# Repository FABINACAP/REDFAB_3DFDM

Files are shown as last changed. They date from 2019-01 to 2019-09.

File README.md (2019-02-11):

# REDFAB_3DFDM
REDFAB 3D FDM, es la primera impresora de la familia REDFAB. Diseñada y fabricada por el equipo de Fab INACAP. Es una impresora de código abierto, disponible para cualquier persona que quiera aprender e introducirse en el mundo de la fabricación digital.

El corazón de la REDFAB se compone de un Ardunio Mega , Ramps versión 1.4/1.5, 4 driver Pololu A4988 y manejado bajo el excelente Firmware Marlin V2.0.

Su estructura es de MDF3mm y un set de piezas impresas en PLA.
La REDFAB 3d FDM, se encuentra siempre en mejora continua.

impresoras

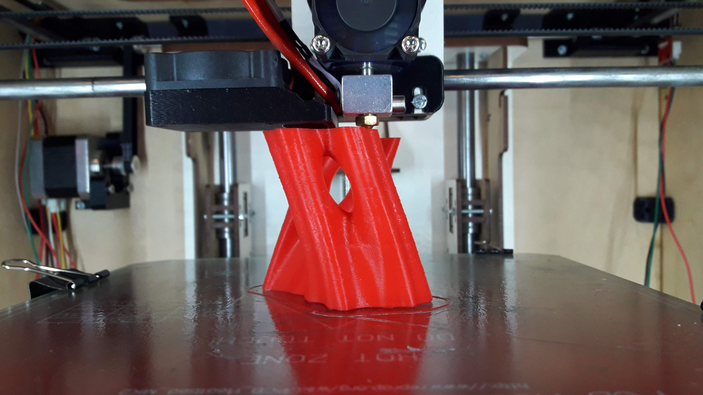
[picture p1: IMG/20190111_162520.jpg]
Test


Una impresora 3D desarrollada por el equipo de Fab INACAP CC-BY-SA-4.0 / An open source 3D printer developed by Fab INACAP team CC-BY-SA-4.0.

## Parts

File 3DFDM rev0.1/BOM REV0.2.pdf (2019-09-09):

# BOM REDFAB 3D FDM

V1.1

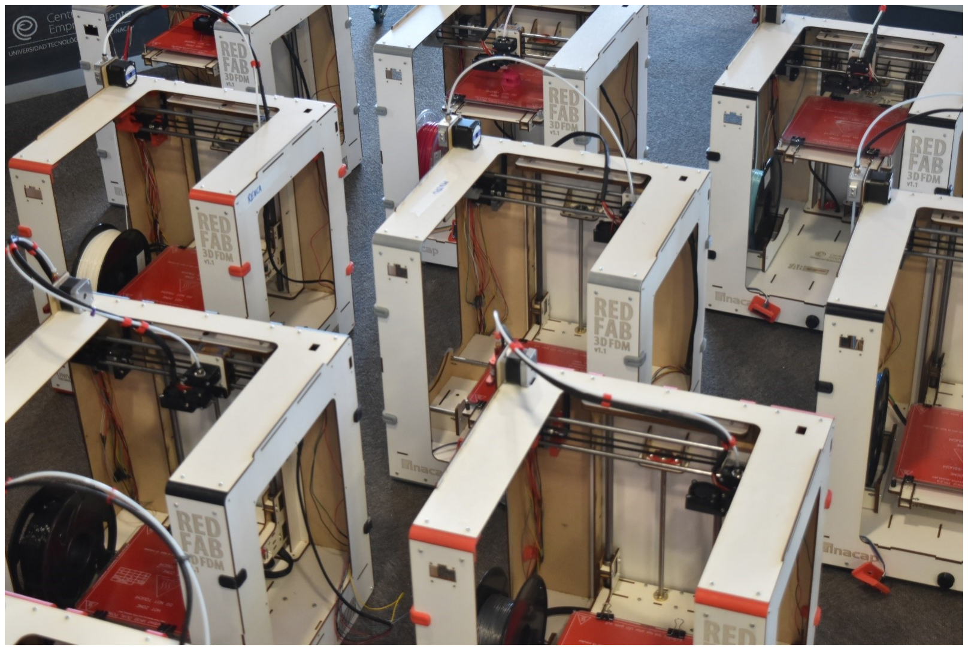
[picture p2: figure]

## Inacap

fabinacap@inacap.cl

### Lista de componentes mecánicos, electrónicos e imprimibles REDFAB 3D FDM v1.1

COMPONENTES MECÁNICOS | CANTIDAD | ITEM
685ZZ, Rodamiento de bolas (5 x 11 x 5mm) | 4
623ZZ, Rodamiento de bolas (3 x 10 x 4mm) | 6
Base Vidrio 21.5 x 21.5cm, e=4mm, chaflan 1cm | 1
LM08UU, Rodamiento lineal de bolas recirculantes (8mm) | 8
LM12UU, Rodamiento lineal de bolas recirculantes (12mm) | 4
Polea dentada GT2-16 (16 dientes) (D.I. 5mm) (B máx: 6mm) | 5
Correa dentada GT2-6 (goma con refuerzo fibra de vidrio) | 3mt
Correa cerrada GT2-6 200mm (goma con refuerzo fibra de vidrio) | 1
Varilla Roscada (husillo) 8mm x 300mm + Tuerca Tr8*4 | 1
Acople rígido de aluminio (5mm a 8mm) | 1
Resorte para cama caliente (ID=5mm, OD=7.5mm, h=20mm) | 4
Conector tubo neumático (para tubo pasante) PC4-01 | 1
Tubo teflón (OD=4mm, ID=2mm), Longitud 1 metro | 1
Tuerca M3 para apretar con la mano | 4
Barra acero trefilado (calidad 1020) 8mm x 385mm (+0.00 -2.00mm) | 2
Barra acero trefilado (calidad 1020) 8mm x 400mm (+0.00 -2.00mm) | 2

## Inacap

fabinacap@inacap.cl

Barra acero trefilado (calidad 1020) 12mm x 400mm (+0.00 -2.00mm) | 2
Barra redonda acero plata 5mm x 390mm (+1.00 -2.00mm) | 1
Durolac Blanco MDF 3mm (cortado en trozos 80x130cm) | 1
Clip doble 15mm, pequeños para fijación de base de vidrio | 4
Amarra Cable 2,5mm largo 140 color negro (Pack 25un) | 1
Pernos y Tuercas | CANTIDAD | ITEM
Tuercas M3 | 150
Pernos Cocina Cabeza Punta cruz M3x10 | 30
Pernos Cocina Cabeza Punta cruz M3x12 | 30
Pernos Cocina Cabeza Punta cruz M3x15 | 30
Pernos Cocina Cabeza Punta cruz M3x20 | 30
Pernos Cocina Cabeza Punta cruz M3x25 | 30
Pernos Cocina Cabeza Punta cruz M3x30 | 30
Pernos Cocina Cabeza Punta cruz M3x35 | 10
Pernos Parker Cabeza Cilíndrica M3x15 | 3
Pernos Cocina Cabeza Punta cruz M4x10 | 4
Golilla Plana Zincada M3 | 10

## Inacap

fabinacap@inacap.cl

COMPONENTES ELECTRÓNICOS | CANTIDAD | ITEM
Arduino Mega 2560 R3 (versión compatible) | 1
Ramps 1.5 o superior | 1
A4988, driver motor paso a paso | 5
Motor PAP bipolar NEMA 17 (3,45V, 1.5A, 45N.cm, 1.8°) Cable 1m removible | 4
Pantalla LCD Oled 1.3" I2C, color blanco | 1
Módulo lector tarjetas SD | 1
Módulo encoder rotatorio | 1
Final de carrera horizontal con PCB + cables | 3
Cama caliente 214 x 214 mm MK2 (Voltaje entrada 12V o 24V) | 1
Termistor NTC 100K 3950 con cable 1 metro | 2
Ventilador 4010 12V (40x40x10mm) | 3
MK8 extrusor remoto de aleación de aluminio para filamento 1.75mm | 1
Fuente Meanwell LRS-350-12 (12V, 29A, 350W) | 1
Conector C14 interruptor con fusible 220V 2A | 1
Cable de poder para PC 1.5m | 1

## Inacap

fabinacap@inacap.cl

COMPONENTES ELECTRÓNICOS | CANTIDAD | ITEM
Cable USB B macho a USB A B hembra para montaje 30cm | 1
Cable USB 2.0 cobre TIPO A-B impresora 1.5m | 1
Diodo 1N4004 o 1N4008 | 2
Extrusor E3D V6 + Ventilador, Boquilla 0,4mm 1,75mm | 1
Memoria SD 8Gb clase 10 | 1
Manga trenzada para cables (8mm expandible) | 3mt
Pack 127 fundas termo retráctiles varios tamaños | 1
Terminal Faston hembra (azul) | 10
Terminal Horquilla 4.4mm (azul) | 10
Pack 40 cables Dupont hembra 30cm | 1
Cordon 3x0.75mm2 | 0.5mt
Cable Evaflex H07Z21-K 2.5mm, (2m color rojo, 2m color verde) | 4mt
Cable AWG 26 colores rojo, negro, gris, amarillo, verde, blanco. (3mt de c/u) | 18mt
Cable AWG 20 (color rojo) | 3mt
Cabezal 2 pines para conector Dupont (paso 2.54mm) | 10
Cabezal 3 pines para conector Dupont (paso 2.54mm) | 10

## Inacap

fabinacap@inacap.cl

Cabezal 4 pines para conector Dupont (paso 2.54mm) | 10
Conectores Dupont hembra (paso 2.54mm) (terminales) | 100
Filamento 1kg PLA 1,75mm (color a elección) | 1

## Inacap

fabinacap@inacap.cl

COMPONENTES IMPRESOS PLA, color a elección | CANTIDAD | ITEM
Eje_X_polea • Imprimir con soporte • Altura de capa 0.2mm • Numero de paredes 3 • Capas Inferior/Superior 4 • Relleno 25%) | 1
Eje_X_Soporte_Motor • Imprimir con soporte • Altura de capa 0.2mm • Numero de paredes 3 • Capas Inferior/Superior 4 • Relleno 25%) | 1

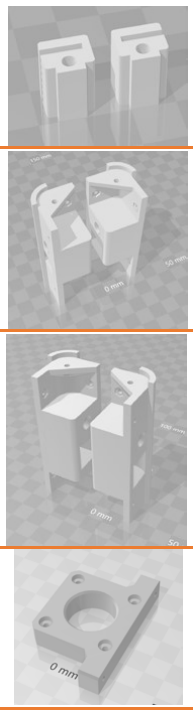
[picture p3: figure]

Tensor Correa un par • Imprimir sin soporte • Altura de capa 0.1mm • Numero de paredes 3 • Capas Inferior/Superior 4 • Relleno 90%) | 1
Eje_Y_Frontal • Imprimir con soporte • Altura de capa 0.2mm • Numero de paredes 3 • Capas Inferior/Superior 4 • Relleno 25%) | 1
Eje_Y_Posterior • Imprimir con soporte • Altura de capa 0.2mm • Numero de paredes 3 • Capas Inferior/Superior 4 • Relleno 25%) | 1
Soporte_Motor_Y • Imprimir sin soporte • Altura de capa 0.2mm • Numero de paredes 3 • Capas Inferior/Superior 4 • Relleno 25%) | 1

## Inacap

fabinacap@inacap.cl

Union_Marcos_Inferior • Imprimir sin soporte • Altura de capa 0.2mm • Numero de paredes 3 • Capas Inferior/Superior 4 • Relleno 25%) | 4
Union_Marcos_posterior • Imprimir sin soporte • Altura de capa 0.2mm • Numero de paredes 3 • Capas Inferior/Superior 4 • Relleno 25%) | 1
Carro_Cabezal • Imprimir sin soporte • Altura de capa 0.2mm • Numero de paredes 3 • Capas Inferior/Superior 4 • Relleno 25%) | 1
Tensor_Correa_Cabezal • Imprimir sin soporte • Altura de capa 0.1mm • Numero de paredes 3 • Capas Inferior/Superior 4 • Relleno 100%) | 1
Soporte_FAN_Layer • Imprimir sin soporte (Recomendación Imprimir en ABS) • Altura de capa 0.2mm • Numero de paredes 3 • Capas Inferior/Superior 4 • Relleno 25%) | 1
Soporte_Hotend • Imprimir sin soporte • Altura de capa 0.2mm • Numero de paredes 3 • Capas Inferior/Superior 4 • Relleno 25%) | 1

## Inacap

fabinacap@inacap.cl

Pantalla_Oled 1.3” • Imprimir sin soporte • Altura de capa 0.2mm • Numero de paredes 2 • Capas Inferior/Superior 3 Relleno 25%) | 1
Clamp • Imprimir sin soporte • Altura de capa 0.2mm • Numero de paredes 3 • Capas Inferior/Superior 4 • Relleno 25%) | 1
Conector_de_Planos • Imprimir sin soporte • Altura de capa 0.2mm • Numero de paredes 3 • Capas Inferior/Superior 4 • Relleno 25%) | 8
Polea_rodamientoB623ZZ_V2 • Imprimir con soporte • Altura de capa 0.1mm • Numero de paredes 3 • Capas Inferior/Superior 2 • Relleno 100%) | 3
Clip cable • Imprimir sin soporte • Altura de capa 0.2mm • Numero de paredes 3 • Capas Inferior/Superior 2 • Relleno 25%) | 1
Rueda_Ajuste_Base (opcional, en remplazo de Tuerca M3 para apretar con la mano) • Imprimir sin soporte • Altura de capa 0.2mm • Numero de paredes 3 • Capas Inferior/Superior 4 • Relleno 25%) | 4
Rueda_Encoder • Imprimir sin soporte • Altura de capa 0.2mm • Numero de paredes 3 • Capas Inferior/Superior 4 • Relleno 25%) | 1

## Inacap

fabinacap@inacap.cl

End_Stop_X_Soporte
- Imprimir sin soporte
- Altura de capa 0.2mm
- Numero de paredes 2
- Capas Inferior/Superior 4 Relleno 25%)

1

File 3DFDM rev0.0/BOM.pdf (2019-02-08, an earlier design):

# BOM REDFAB 3D FDM

V1.1


## Inacap

fabinacap@inacap.cl

### Lista de componentes mecánicos, electrónicos e imprimibles REDFAB 3D FDM v1.1

COMPONENTES MECÁNICOS | CANTIDAD | ITEM
KFL08, Soporte ovalado con rodamiento (8mm) | 2
685ZZ, Rodamiento de bolas (5 x 11 x 5mm) | 2
623ZZ, Rodamiento de bolas (3 x 10 x 4mm) | 6
Base Vidrio 21.5 x 21.5cm, e=4mm, chaflan 1cm | 1
LM08UU, Rodamiento lineal de bolas recirculantes (8mm) | 8
LM12UU, Rodamiento lineal de bolas recirculantes (12mm) | 4
Polea dentada GT2-16 (16 dientes) (D.I. 5mm) (B máx: 6mm) | 5
Correa dentada GT2-6 (goma con refuerzo fibra de vidrio) | 3mt
Correa cerrada GT2-6 200mm (goma con refuerzo fibra de vidrio) | 1
Varilla Roscada (husillo) 8mm x 300mm + Tuerca Tr8*4 | 1
Acople rígido de aluminio (5mm a 8mm) | 1
Resorte para cama caliente (ID=5mm, OD=7.5mm, h=20mm) | 4
Conector tubo neumático (para tubo pasante) PC4-01 | 1
Tubo teflón (OD=4mm, ID=2mm), Longitud 1 metro | 1
Tuerca M3 para apretar con la mano | 4

## Inacap

fabinacap@inacap.cl

Barra acero trefilado (calidad 1020) 8mm x 385mm (+0.00 -2.00mm) | 2
Barra acero trefilado (calidad 1020) 8mm x 400mm (+0.00 -2.00mm) | 2
Barra acero trefilado (calidad 1020) 12mm x 400mm (+0.00 -2.00mm) | 2
Barra redonda acero plata 5mm x 360mm (+1.00 -2.00mm) | 1
Durolac Blanco MDF 3mm (cortado en trozos 80x130cm) | 1
Clip doble 15mm para fijación de base de vidrio | 4
Amarra Cable 2,5mm largo 140 color negro (Pack 25un) | 1

## Inacap

fabinacap@inacap.cl

Pernos y Tuercas | CANTIDAD | ITEM
Tuercas M3 | 150
Tuercas M5 | 4
Pernos Cocina Cabeza Punta cruz M3x10 | 30
Pernos Cocina Cabeza Punta cruz M3x12 | 30
Pernos Cocina Cabeza Punta cruz M3x15 | 30
Pernos Cocina Cabeza Punta cruz M3x20 | 30
Pernos Cocina Cabeza Punta cruz M3x25 | 30
Pernos Cocina Cabeza Punta cruz M3x30 | 30
Pernos Cocina Cabeza Punta cruz M3x35 | 10
Pernos Parker Cabeza Cilíndrica M3x15 | 3
Pernos Cocina Cabeza Punta cruz M4x10 | 4
Pernos Cocina Cabeza Punta cruz M5x12 | 4
Golilla Plana Zincada M3 | 20

## Inacap

fabinacap@inacap.cl

COMPONENTES ELECTRÓNICOS | CANTIDAD | ITEM
Arduino Mega 2560 R3 (versión compatible) | 1
Ramps 1.4 o superior | 1
A4988, driver motor paso a paso | 5
Motor PAP bipolar NEMA 17 (3,45V, 1.5A, 45N.cm, 1.8°) Cable 1m removible | 4
Pantalla LCD Oled 1.3" I2C, color blanco | 1
Módulo lector tarjetas SD | 1
Módulo encoder rotatorio | 1
Final de carrera horizontal con PCB + cables | 3
Cama caliente 214 x 214 mm MK2 (Voltaje entrada 12V o 24V) | 1
Termistor NTC 100K 3950 con cable 1 metro | 2
Ventilador 4010 12V (40x40x10mm) | 3
MK8 extrusor remoto de aleación de aluminio para filamento 1.75mm | 1
Fuente Meanwell LRS-350-12 (12V, 29A, 350W) | 1
Conector C14 interruptor con fusible 220V 2A | 1
Cable de poder para PC 1.5m | 1

## Inacap

fabinacap@inacap.cl

COMPONENTES ELECTRÓNICOS | CANTIDAD | ITEM
Cable USB B macho a USB A B hembra para montaje 30cm | 1
Cable USB 2.0 cobre TIPO A-B impresora 1.5m | 1
Diodo 1N4004 o 1N4008 | 2
Extrusor E3D V6 + Ventilador, Boquilla 0,4mm 1,75mm | 1
Memoria SD 8Gb clase 10 | 1
Manga trenzada para cables (8mm expandible) | 3mt
Pack 127 fundas termo retráctiles varios tamaños | 1
Terminal Faston hembra (azul) | 10
Terminal Horquilla 4.4mm (azul) | 10
Pack 40 cables Dupont hembra 30cm | 1
Cordon 3x0.75mm2 | 0.5mt
Cable Evaflex H07Z21-K 2.5mm, (2m color rojo, 2m color verde) | 4mt
Cable AWG 26 colores rojo, negro, gris, amarillo, verde, blanco. (3mt de c/u) | 18mt
Cable AWG 20 (color rojo) | 3mt
Cabezal 2 pines para conector Dupont (paso 2.54mm) | 10

## Inacap

fabinacap@inacap.cl

Cabezal 3 pines para conector Dupont (paso 2.54mm) | 10
Cabezal 4 pines para conector Dupont (paso 2.54mm) | 10
Conectores Dupont hembra (paso 2.54mm) (terminales) | 100
Filamento 1kg PLA 1,75mm (color a elección) | 1

## Inacap

fabinacap@inacap.cl

COMPONENTES IMPRESOS PLA, color a elección | CANTIDAD | ITEM
Eje_X_polea • Imprimir con soporte • Altura de capa 0.2mm • Numero de paredes 3 • Capas Inferior/Superior 4 • Relleno 25%) | 1
Eje_X_Soporte_Motor • Imprimir con soporte • Altura de capa 0.2mm • Numero de paredes 3 • Capas Inferior/Superior 4 • Relleno 25%) | 1

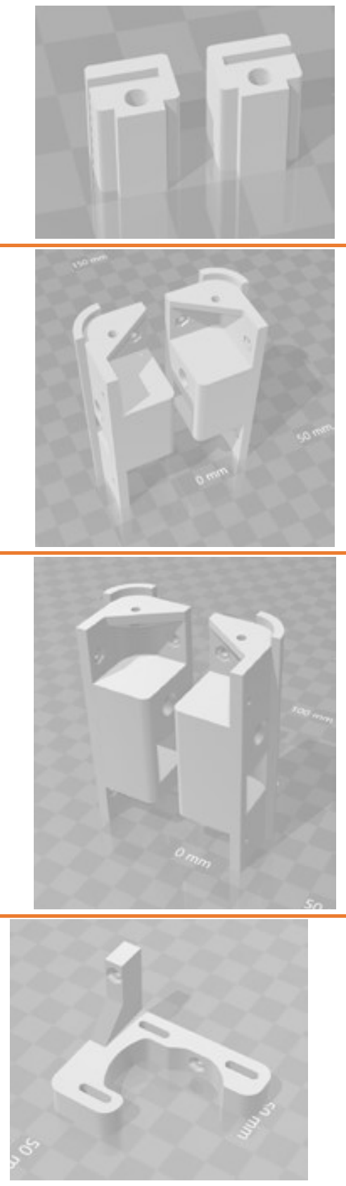
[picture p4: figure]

Tensor Correa un par • Imprimir sin soporte • Altura de capa 0.1mm • Numero de paredes 3 • Capas Inferior/Superior 4 • Relleno 90%) | 1
Eje_Y_Frontal • Imprimir con soporte • Altura de capa 0.2mm • Numero de paredes 3 • Capas Inferior/Superior 4 • Relleno 25%) | 1
Eje_Y_Posterior • Imprimir con soporte • Altura de capa 0.2mm • Numero de paredes 3 • Capas Inferior/Superior 4 • Relleno 25%) | 1
Soporte_Motor_Y • Imprimir sin soporte • Altura de capa 0.2mm • Numero de paredes 3 • Capas Inferior/Superior 4 • Relleno 25%) | 1

## Inacap

fabinacap@inacap.cl

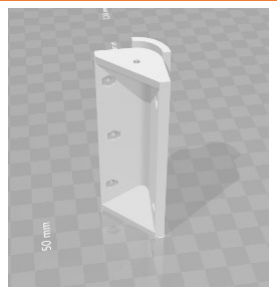
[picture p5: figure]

Union_Marcos_Inferior • Imprimir sin soporte • Altura de capa 0.2mm • Numero de paredes 3 • Capas Inferior/Superior 4 • Relleno 25%) | 4
Union_Marcos_posterior • Imprimir sin soporte • Altura de capa 0.2mm • Numero de paredes 3 • Capas Inferior/Superior 4 • Relleno 25%) | 3
Carro_Cabezal • Imprimir sin soporte • Altura de capa 0.2mm • Numero de paredes 3 • Capas Inferior/Superior 4 • Relleno 25%) | 1
Tensor_Correa_Cabezal • Imprimir sin soporte • Altura de capa 0.1mm • Numero de paredes 3 • Capas Inferior/Superior 4 • Relleno 100%) | 1
Soporte_FAN_Layer • Imprimir sin soporte (Recomendación Imprimir en ABS) • Altura de capa 0.2mm • Numero de paredes 3 • Capas Inferior/Superior 4 • Relleno 25%) | 1
Soporte_Hotend • Imprimir sin soporte • Altura de capa 0.2mm • Numero de paredes 3 • Capas Inferior/Superior 4 • Relleno 25%) | 1
Clamp • Imprimir sin soporte • Altura de capa 0.2mm • Numero de paredes 3 • Capas Inferior/Superior 4 • Relleno 25%) | 1

## Inacap

fabinacap@inacap.cl

Conector_de_Planos • Imprimir sin soporte • Altura de capa 0.2mm • Numero de paredes 3 • Capas Inferior/Superior 4 • Relleno 25%) | 8

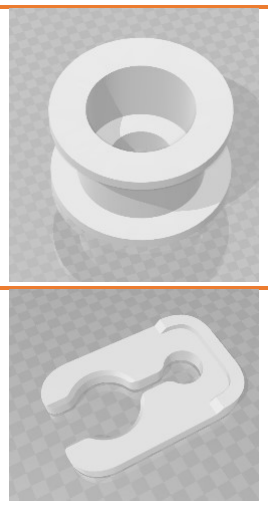
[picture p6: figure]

Polea_rodamientoB623ZZ_V2 • Imprimir con soporte • Altura de capa 0.1mm • Numero de paredes 3 • Capas Inferior/Superior 2 • Relleno 100%) | 3
Clip Bowden • Imprimir sin soporte • Altura de capa 0.1mm • Numero de paredes 3 • Capas Inferior/Superior 2 • Relleno 100%) | 2
Clip cable • Imprimir sin soporte • Altura de capa 0.2mm • Numero de paredes 3 • Capas Inferior/Superior 2 • Relleno 25%) | 1

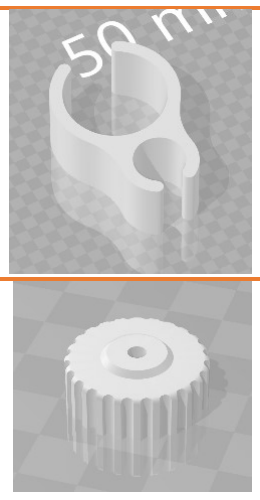
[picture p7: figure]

Clip PTFE • Imprimir sin soporte • Altura de capa 0.1mm • Numero de paredes 3 • Capas Inferior/Superior 2 • Relleno 100%) | 5
Rueda_Ajuste_Base (opcional, en remplazo de Tuerca M3 para apretar con la mano) • Imprimir sin soporte • Altura de capa 0.2mm • Numero de paredes 3 • Capas Inferior/Superior 4 • Relleno 25%) | 4
Rueda_Encoder • Imprimir sin soporte • Altura de capa 0.2mm • Numero de paredes 3 • Capas Inferior/Superior 4 • Relleno 25%) | 1

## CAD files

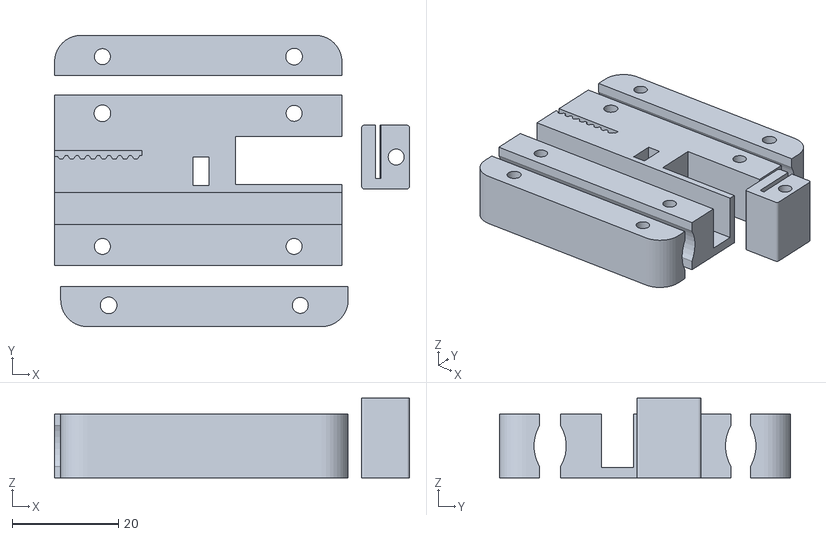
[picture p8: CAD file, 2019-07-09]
3DFDM rev0.1/STL/Carro X/Carro.stl
66.7 x 54.7 x 15.0

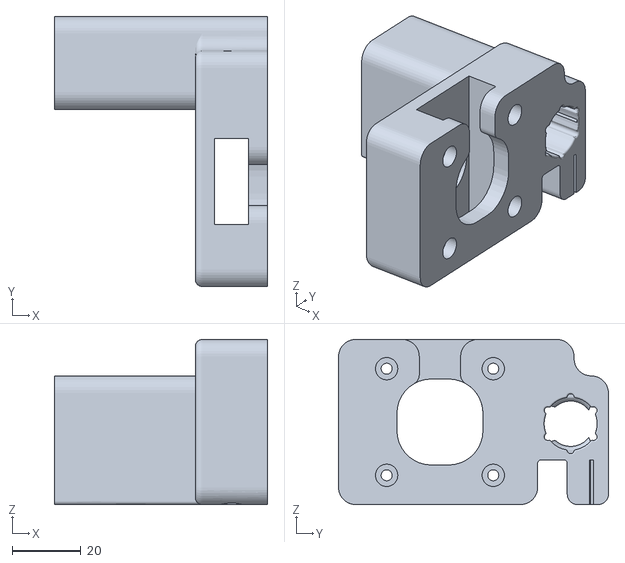
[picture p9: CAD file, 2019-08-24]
3DFDM rev0.1/STL/Eje_X/Eje_X_Soporte_Motor.stl
62.0 x 78.5 x 48.0

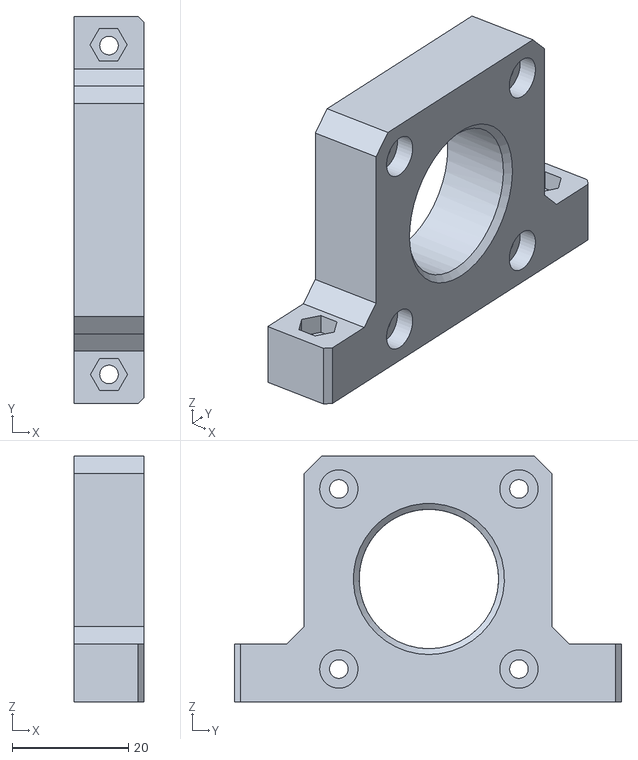
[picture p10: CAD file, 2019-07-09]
3DFDM rev0.1/STL/Eje_Y/Soporte_Motor_v2.STL
12.0 x 66.6 x 42.3

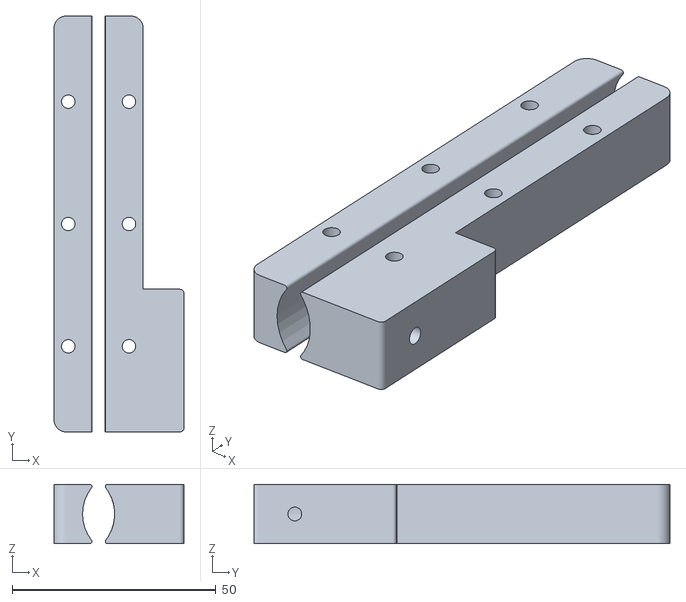
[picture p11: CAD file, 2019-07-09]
3DFDM rev0.1/STL/Eje_Z/Eje_Z_Separadores.stl
31.9 x 102.0 x 14.5

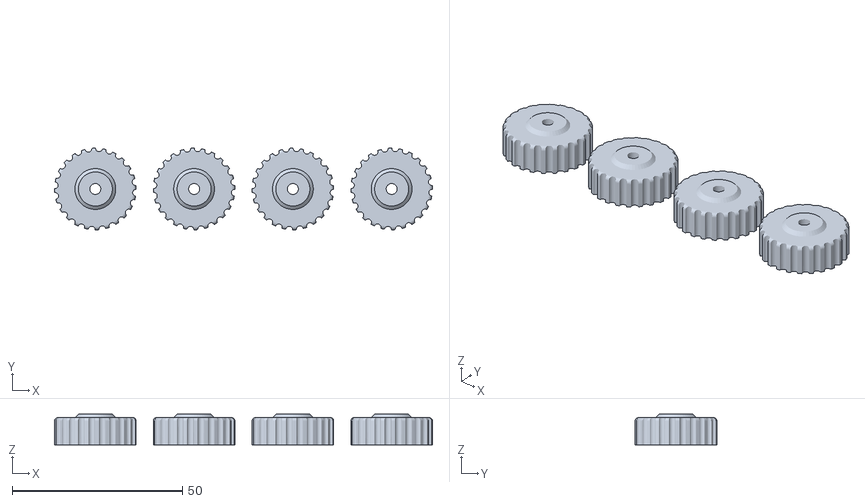
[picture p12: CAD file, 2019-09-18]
3DFDM rev0.1/STL/Otros/4xRueda_Ajuste_Base.stl
111.0 x 24.0 x 9.00

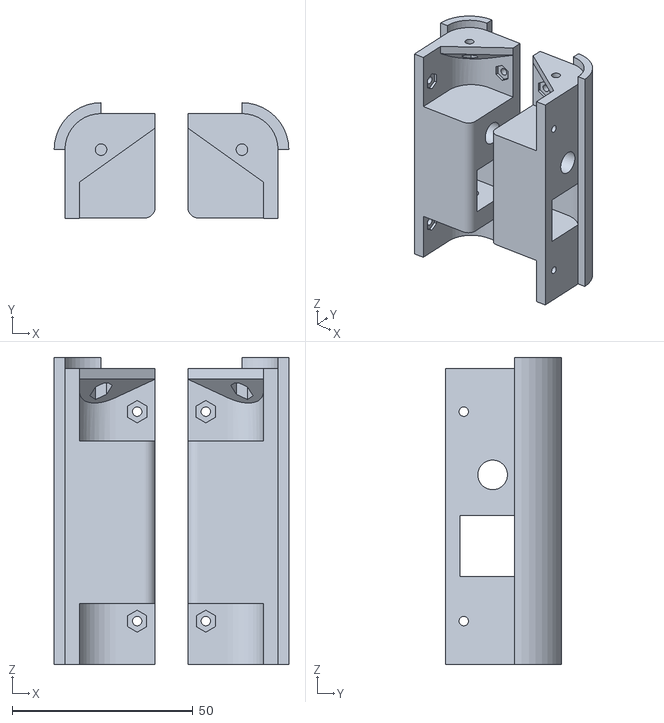
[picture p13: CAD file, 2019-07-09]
3DFDM rev0.1/STL/Eje_Y/Eje_Y_Posterior_V2.stl
65.0 x 32.0 x 85.0

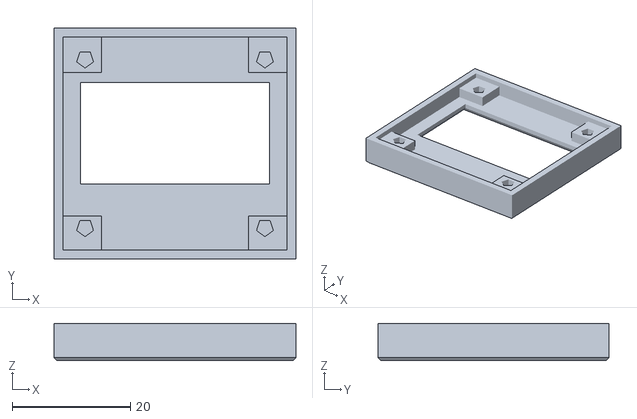
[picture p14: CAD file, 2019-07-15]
3DFDM rev0.1/STL/Otros/OLED-Test.stl
40.9 x 39.0 x 6.30

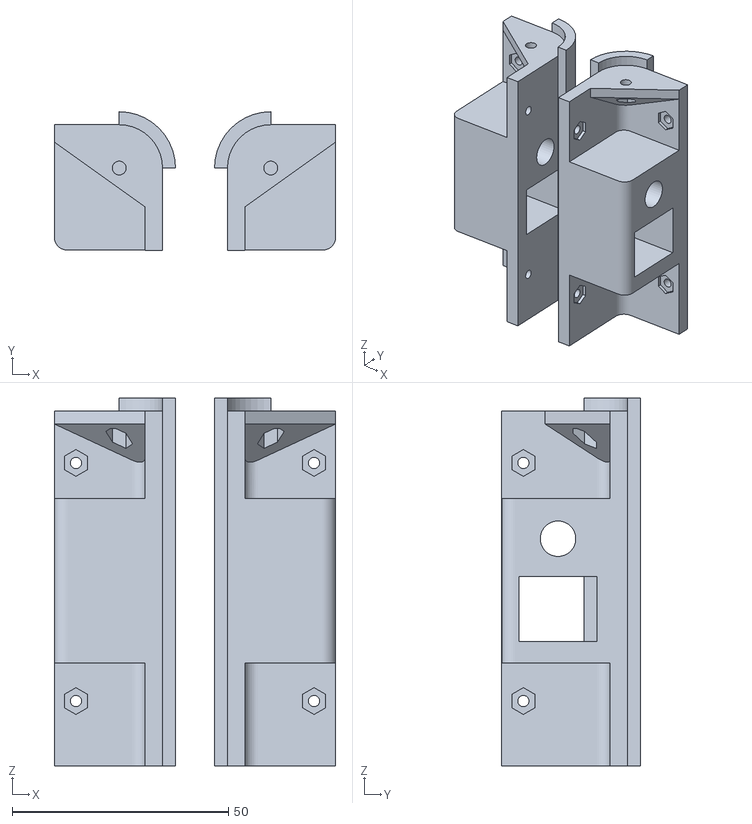
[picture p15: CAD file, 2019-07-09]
3DFDM rev0.1/STL/Eje_Y/Eje_Y_Frontal_V2.stl
65.0 x 32.0 x 85.0

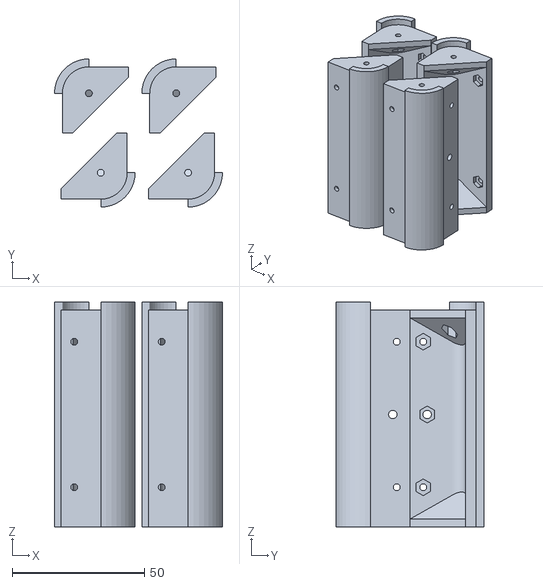
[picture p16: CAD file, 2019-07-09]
3DFDM rev0.1/STL/Otros/4xUnion_Marcos_Inferior.stl
63.5 x 56.0 x 85.0

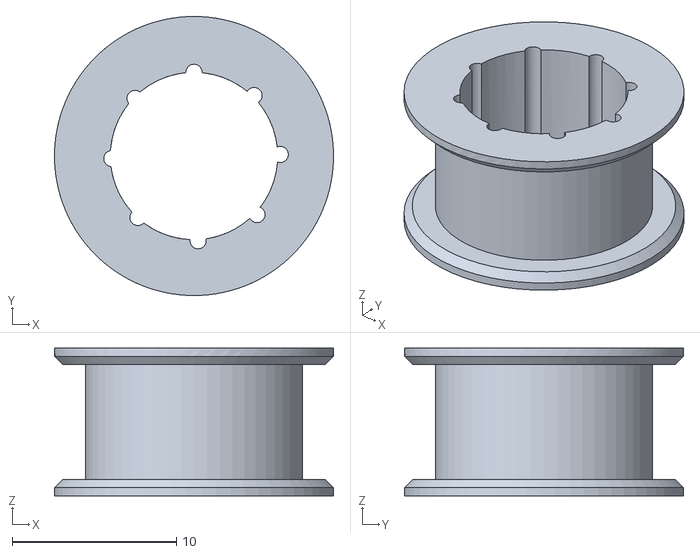
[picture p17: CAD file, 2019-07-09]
3DFDM rev0.1/STL/Otros/Polea_rodamientoB623ZZ_V3.STL
17.0 x 17.0 x 9.00

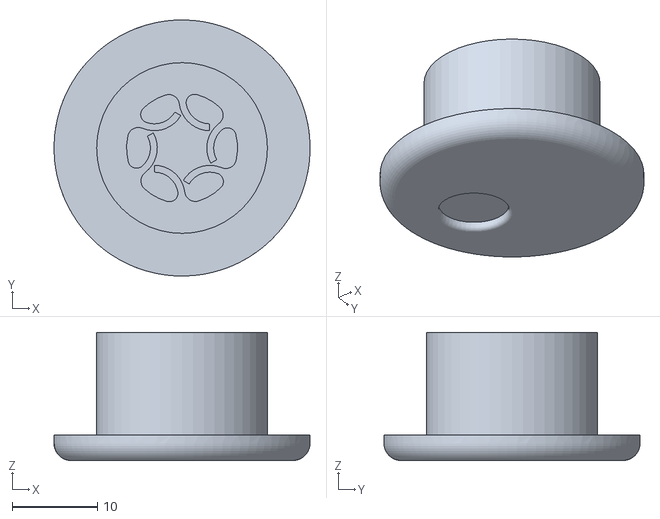
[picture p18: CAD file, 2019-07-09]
3DFDM rev0.1/STL/Otros/Rueda_Encoder.stl
30.0 x 30.0 x 15.0

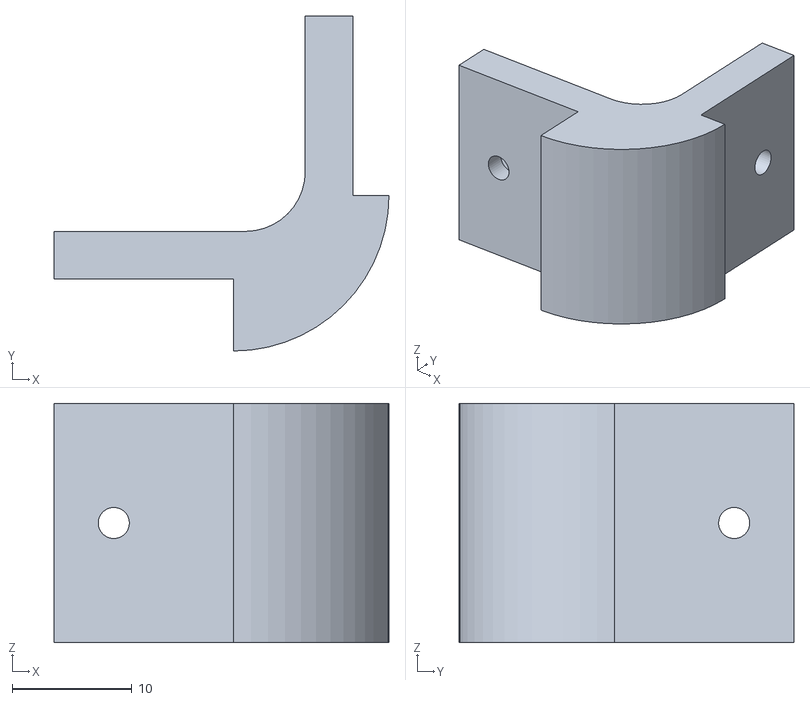
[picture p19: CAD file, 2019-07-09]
3DFDM rev0.1/STL/Otros/Union_Marcos_posterior.stl
28.0 x 28.0 x 20.0

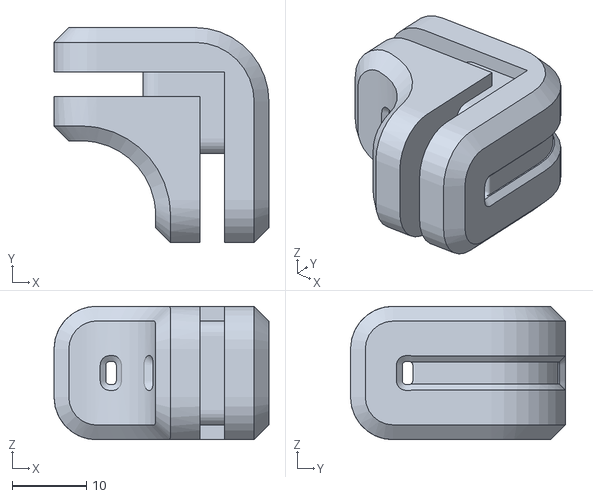
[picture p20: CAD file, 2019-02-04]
3DFDM rev0.1/STL/Otros/Conector de Planos.stl
29.0 x 29.0 x 18.0

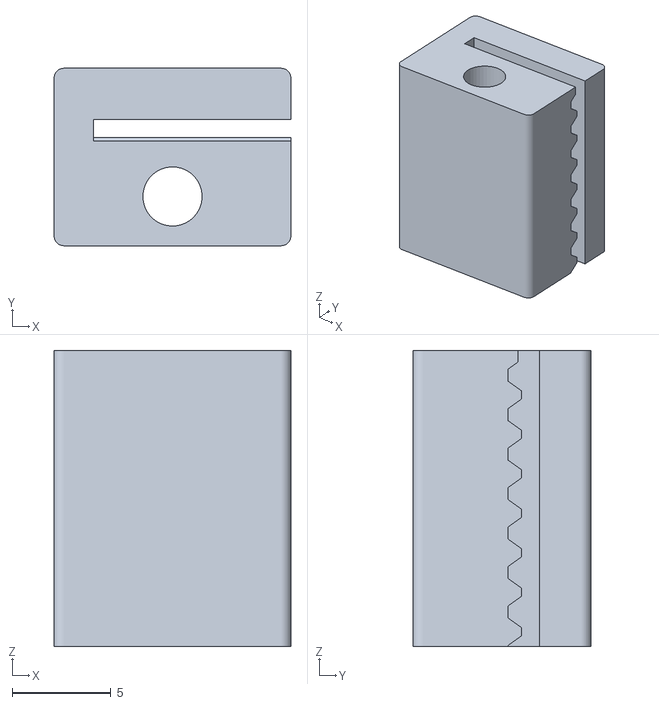
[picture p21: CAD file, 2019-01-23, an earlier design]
3DFDM rev0.0/CAD/STL/CARRO_CABEZAL/Tensor_correa_Carro.STL
12.0 x 9.00 x 15.0

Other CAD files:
3DFDM rev0.0/CAD/STL/EJE X/Eje_X_polea.stl
3DFDM rev0.0/CAD/STL/EJE Y/Eje_Y_Der_Frontal.stl
3DFDM rev0.0/CAD/STL/EJE Z/EndstopZ.stl
3DFDM rev0.0/CAD/STL/Otros/Polea_rodamientoB623ZZ_V2.STL
3DFDM rev0.0/CAD/STL/CARRO_CABEZAL/Carro.STL
3DFDM rev0.0/CAD/STL/EJE X/Eje_X_Soporte_Motor.stl
3DFDM rev0.0/CAD/STL/EJE X/Soporte_EndStop_X.stl
3DFDM rev0.0/CAD/STL/EJE X/Tensor Correa.stl
3DFDM rev0.0/CAD/STL/EJE Y/Eje_Y_Der_Posterior.stl
3DFDM rev0.0/CAD/STL/EJE Y/Eje_Y_Izq_Frontal.stl
3DFDM rev0.0/CAD/STL/EJE Y/Eje_Y_Izq_Posterior.stl
3DFDM rev0.0/CAD/STL/EJE Y/Soporte_EndStop_Y.stl
3DFDM rev0.0/CAD/STL/EJE Y/Soporte_Motor.STL
3DFDM rev0.0/CAD/STL/Otros/Clip Bowden.stl
3DFDM rev0.0/CAD/STL/Otros/Clip PTFE.stl
3DFDM rev0.0/CAD/STL/Otros/Clip cable.stl
3DFDM rev0.0/CAD/STL/Otros/Rueda_Ajuste_Base.stl
3DFDM rev0.0/CAD/STL/Otros/Rueda_Encoder.stl
3DFDM rev0.0/CAD/STL/Otros/Union_Marcos_Inferior.STL
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

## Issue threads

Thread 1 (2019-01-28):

Indicaciones por piezas a imprimir

fprietorossi, 2019-01-28:
Estimados.
Se encuentran las piezas imprimibles de la maquina, pero debería existir una pequeña descripción de requerimientos para cada una de ellas, por ejemplo, ubicación en la cama de impresión (para evitar que se rompa bajo tensión), nivel de relleno, cantidad de impresiones de cada pieza, etc.

FABINACAP, 2019-02-03:
Estimado Francisco, muchas gracias por su comentario.
Estamos trabajando en la documentación necesaria para que el armado sea mas claro y preciso.
Se actualizo lista de archivos y  BOM donde se indica el total de componentes impresos y configuraciones recomendadas.
Saludos.

fprietorossi, 2019-03-06:
Excelente, está desarrollándose muy bien

Closed 2019-03-06.

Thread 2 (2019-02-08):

firmware

jaimereyesc, 2019-02-08:
hola, podrian subir los archivos de los firmware que instalamos en la capacitacion al final, cuando terminamos las maquinas. ya que las 2 que llegaron a mi sede (Maipú) venian con una version muy distinta a la que usamos y ademas descalibradas.
esto ya que lo mas probable es que no sea el unico al que le pase, y asi tener una forma de setearlas.

gracias

FABINACAP, 2019-02-11:
Estimado Jaime.
FW para impresora se encuentra subido en el repositorio.
En relación a la calibración, esto es algo que va a ocurrir siempre, es parte del proceso de aprendizaje y de mojara continua ;)
Saludos

jaimereyesc, 2019-02-11:
gracias por subirla
saludos

fprietorossi, 2019-02-12:
Para poder compilar el firmware, se necesita tener en el equipo la librería U8glib_Arduino, la cual se puede descargar desde https://github.com/olikraus/U8glib_Arduino/releases

fprietorossi, 2019-02-12:
Compila mejor usando el IDE de Arduino 1.9.0 BETA (Descarga en https://www.arduino.cc/download_handler.php)  para evitar el problema de error por nombre del archivo o extensión muy largo que aparece en la versión 1.8.x

FABINACAP, 2019-03-08:
Si nadie mas tiene dudas por lo comentado.. se cierra este tema.
gracias Francisco por el aporte.-

Closed 2019-03-08.

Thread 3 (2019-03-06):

Instrucciones de Armado de Piezas

fprietorossi, 2019-03-06:
Existe el esquema de las piezas que son cortadas para el armado de la máquina
Se agradecería un set de imágenes o indicativo para el armado de ellas, junto a que piezas impresas deben usarse

FABINACAP, 2019-03-08:
Francisco... pronto subiremos el manual.
Saludos

elisahonorato, 2021-11-13:
Hola! Al final subieron el manual?

Closed 2019-03-08.

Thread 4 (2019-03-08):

Problema de tracción en filamento

vverav, 2019-03-08:
Estimados:
Tenemos un problema con la tracción del filamento, que "patina" al pasar por las ruedas que deberían impulsarlo al extrusor. La impresora funciona, pero al no poder jalar de manera suave el filamento por momentos comienza a depositar PLA de manera irregular (no líneas, sino que básicamente deja gotas intercaladas con zonas sin material o muy poco).
Un video de cómo el filamento no puede ser impulsado puede ser visto aquí:

https://www.dropbox.com/s/ou4nkrbkag875vo/VID_20190305_161715.mp4?dl=0

Hasta el momento hemos chequeado el motor que lo impulsa y la pieza que se atacha a este (incluso armamos la misma pieza completa con las partes de otra impresora nueva, y el problema continuó), así como estamos seguros que la manguera de silicona efectivamente entra completamente en el extrusor, por lo que no hay roce dentro de este. Tampoco el filamento está trabado o es irregular de algún modo (hemos probado con al menos tres filamentos diferentes). La temperatura del extrusor es la correcta, y dado que por ratos imprime bien no creemos que haya una obstrucción en el cabezal.
Tenemos la duda si podría ser algo relacionado con la potencia del motor, y nos queda probar el montaje completo de un motor de filamento de otra impresora que esté operando correctamente. ¿Qué otras pruebas nos sugieren hacer?
Saludos

FABINACAP, 2019-03-08:
Hola muchachos.. por lo que veo en el video, la perdida de pasos puede estar relacionada mas bien con obstrucción en el cabezal bowden. esto suele ocurrir por diferentes motivos.
les recomiendo retirar el filamento del cabezal ver el estado, verificar que el tubo de teflón llegue correctamente. también revisar los pasos del extrusor.
suban mas imágenes del sistema completo .

https://www.spainlabs.com/foros/tema-GUIA-DEFINITIVA-de-impresion-3d-todos-tus-problemas-resueltos--5081

vverav, 2019-03-08:
Probé si era una obstrucción en el cabezal, pero se me olvidó mencionar un detalle: el filamento resbala incluso cuando el filamento todavía no ha llegado al cabezal cuando se carga. De hecho he notado que si se modifica un poco la presión entre las dos ruedas que impulsan el filamento (se aliviana un poco) la tracción mejora. Seguiré haciendo pruebas para encontrar la causa.

FABINACAP, 2019-03-08:
En base a lo comentado entonces, puede que sea la potencia entregada al motor PAP, recomiendo lo siguiente.
ajustar el potenciometro del pololu A4988. utilizar voltimetro.
una ves calibrado en un valor ref. 0.8-0.85v mover motor extrusor sin tubo de teflon puesto para ver como avanza el filamento.
Saludos

fprietorossi, 2019-03-12:
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

Es un excelente referente de los problemas la guia, podriamos hacernos una para nosotros, del mismo estilo, es decir:
- Problema típico
- Causal
- Posibilidades de solución

Saludos

vverav, 2019-03-12:
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

Hola Chicos. Ajusté el potenciómetro (de 0.80 lo pasé a 0.85), pero sigue presentando el problema, aunque en esta ocasión no lo hizo cuando el filamento estaba en camino al cabezal, sino que una vez que llegó. Haré otras pruebas y veré cómo me va. Puedo montar el motor en otra impresora que está operando correctamente para confirmar/descartar que el problema sea en este elemento y no algo en la extrusión. Les contaré cómo me va...

Closed 2019-07-01.

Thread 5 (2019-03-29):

Problema con calentamiento de cama / boquilla

vverav, 2019-03-29:
Estimados:
Tengo un problema con una de las impresoras, que ha estado sistemáticamente dando problemas de calentamiento de la cama. He probado si la placa envía la señal cuando se le da la orden de calentar (con la cama desconectada) y lo hace, pero al conectar los cables deja de enviar voltaje. Probé la cama que tenía instalada en otra impresora, y la calienta sin problemas, por lo que no está en corte, así como puse en la impresora con problemas una cama que estaba funcionando en otra máquina y el error continua (aunque en un principio funcionó algunas horas). El termistor está bueno, y repasé las conexiones por si había algo desoldado, pero no encontré nada. La luz testigo que tiene la RAMPS actúa según lo esperado, y no enciende cuando el calentamiento de la cama es fallido.
En un principio pensé que podía ser la RAMPS, que había perdido la salida de potencia, pero la cambié por una nueva y no hubo resultados. También pensé que podía ser un problema de la fuente al exigir más corriente, pero la boquilla si la calienta. Ahora, a la RAMPS llegan dos conexiones desde la fuente, pero me imagino que la fuente sólo tiene varios conectores por polo, pero no realmente salidas independientes.
En el caso de la cama, el mensaje es este:

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

En la misma máquina tuve un problema con el calentamiento de la boquilla, e hice pruebas similares, pero resultó que al parecer se había quemado el calefactor, pues al poner una nueva dejó de dar problemas (hasta ahora).
¿Qué más podría probar?

FABINACAP, 2019-04-04:
Este problema se da basicamente por las condiciones ambientales (sistemas de aire acondicionado) por lo tanto recomiendo evitar de alguna manera circulaciones de aire.. esto es fundamental sobre todo para trabajar con materiales como el ABS.-
Saludos,

Closed 2019-04-04.

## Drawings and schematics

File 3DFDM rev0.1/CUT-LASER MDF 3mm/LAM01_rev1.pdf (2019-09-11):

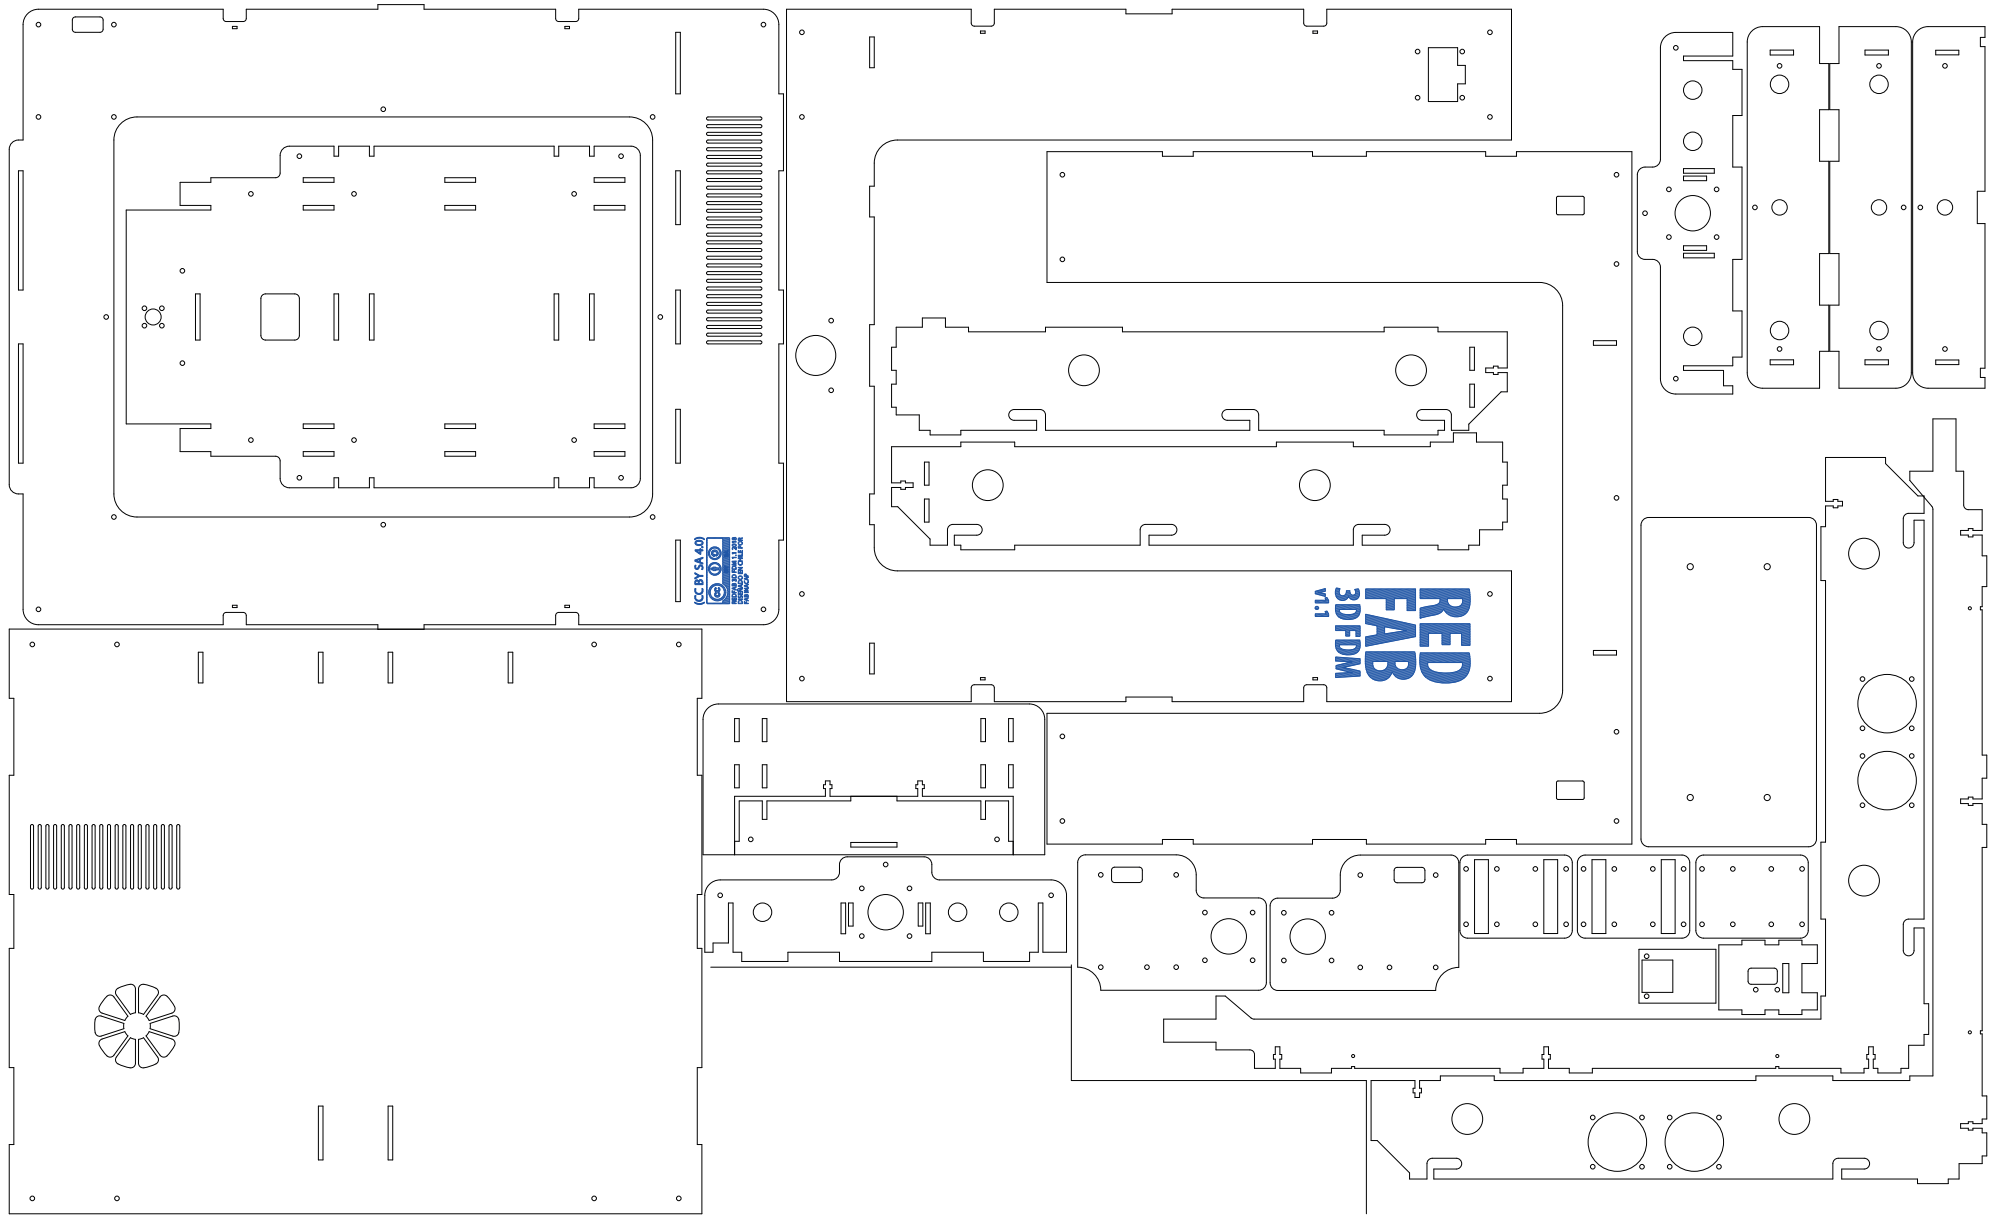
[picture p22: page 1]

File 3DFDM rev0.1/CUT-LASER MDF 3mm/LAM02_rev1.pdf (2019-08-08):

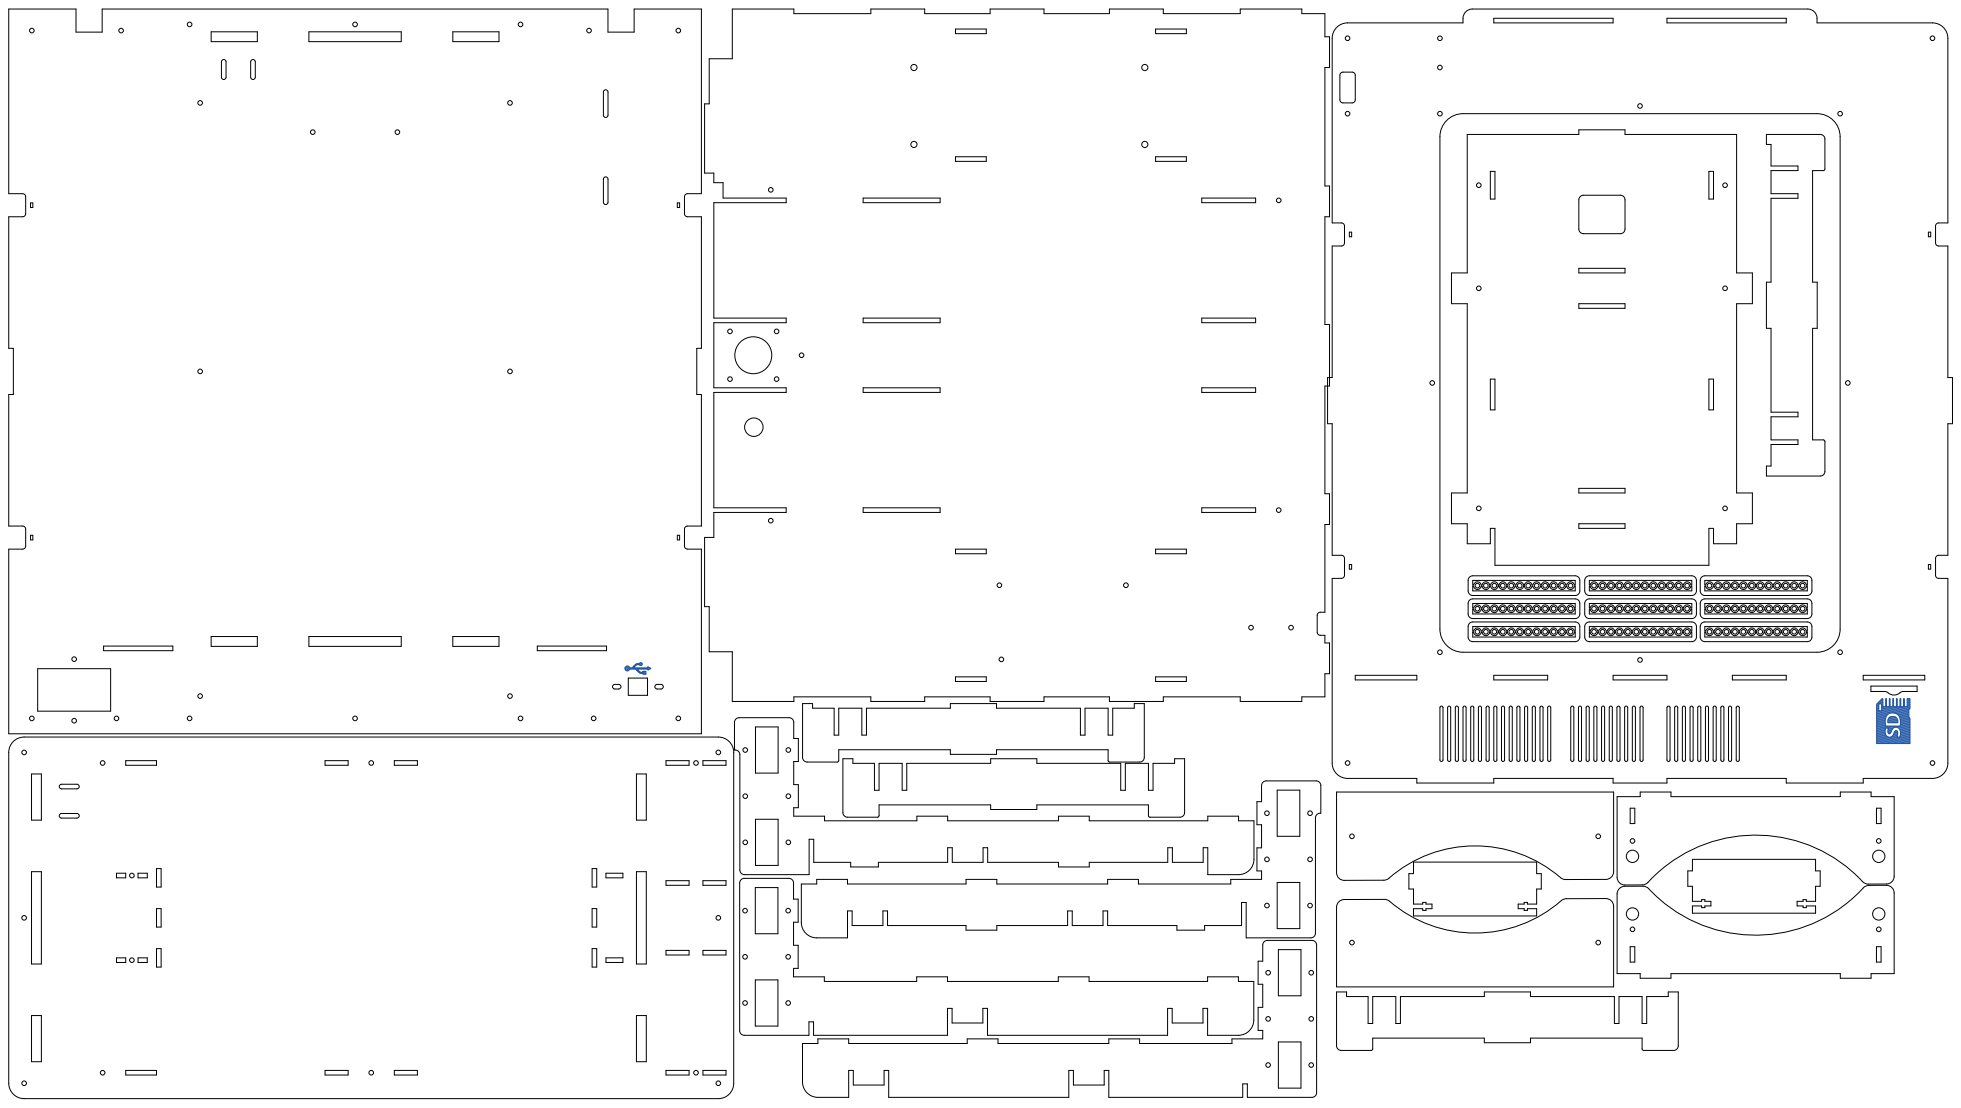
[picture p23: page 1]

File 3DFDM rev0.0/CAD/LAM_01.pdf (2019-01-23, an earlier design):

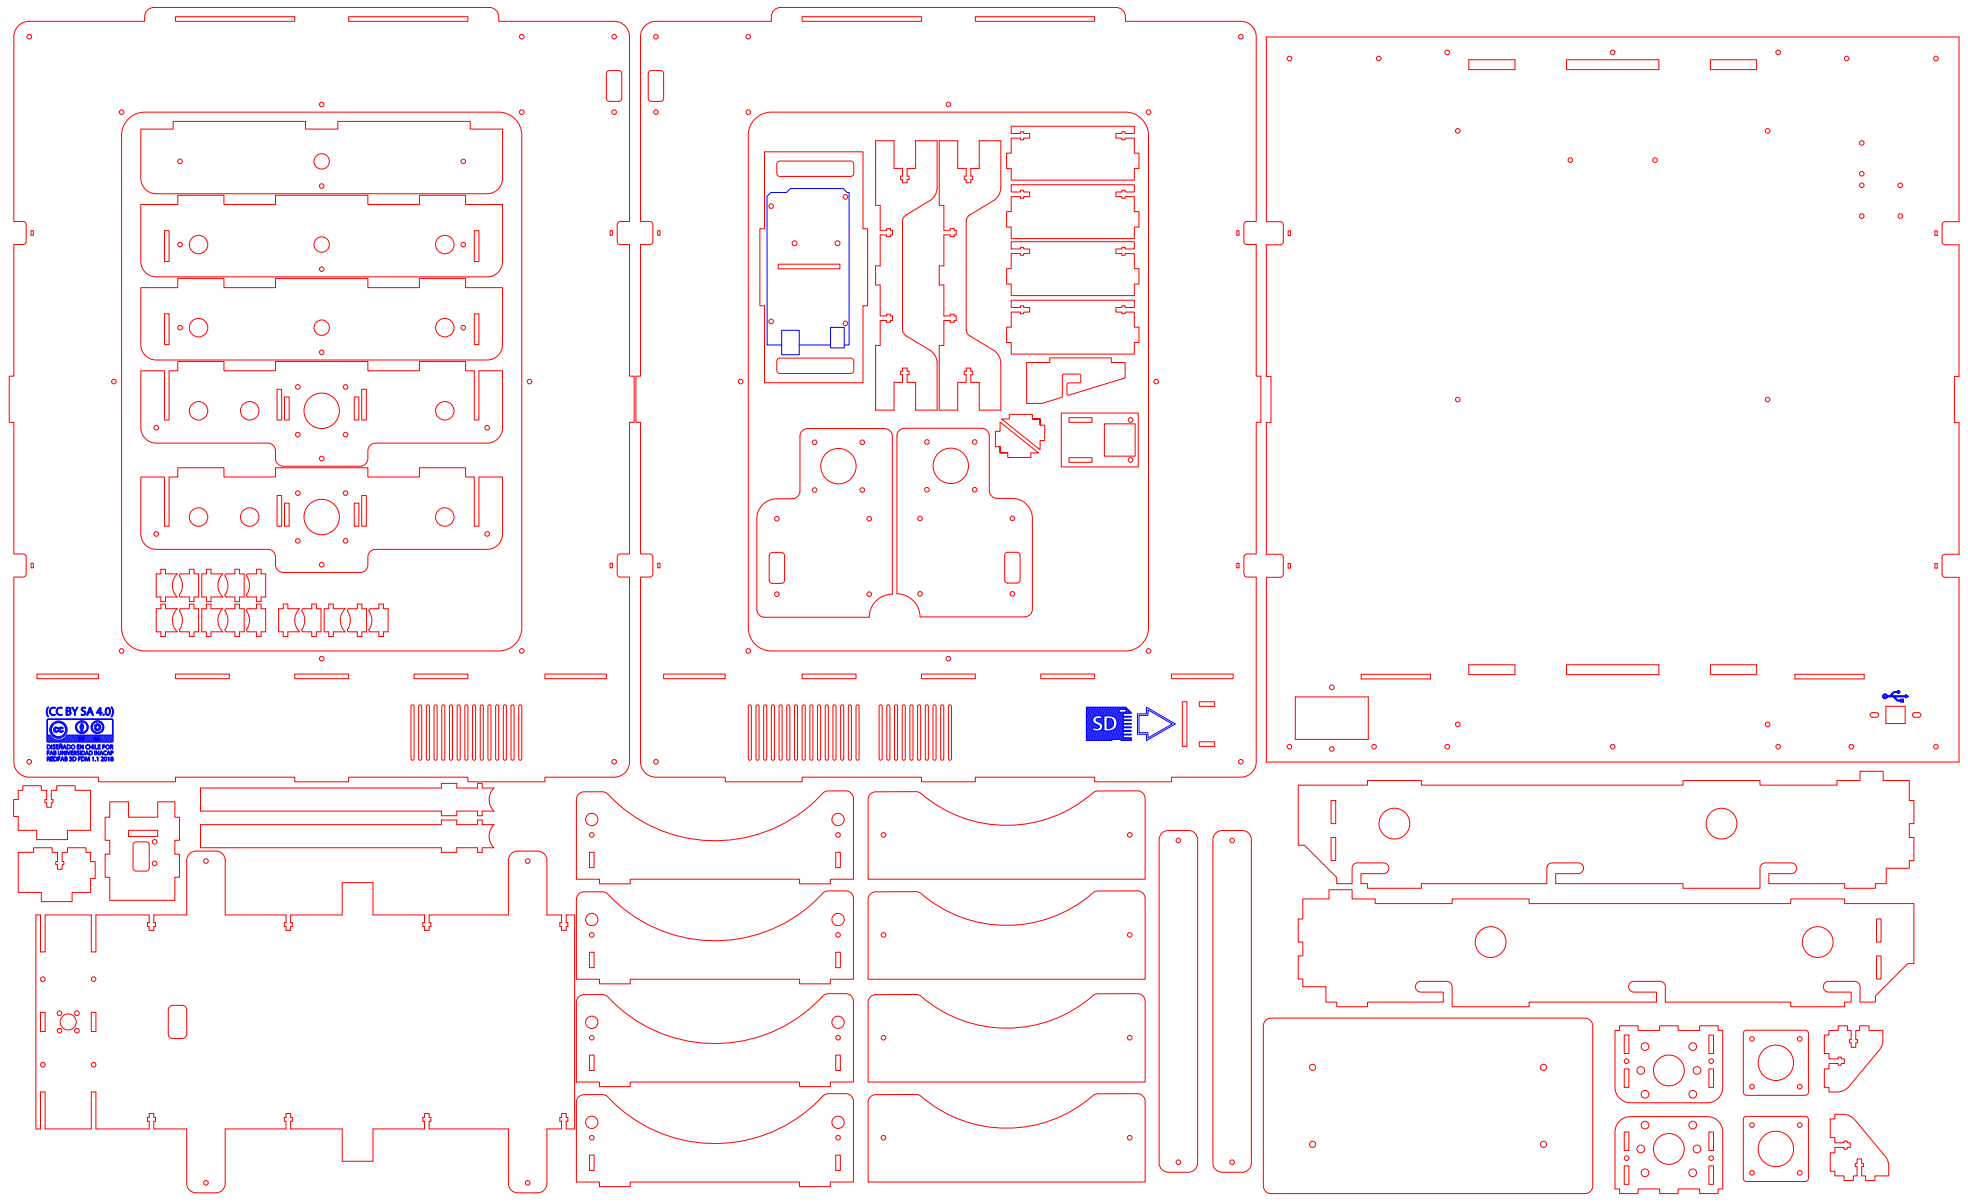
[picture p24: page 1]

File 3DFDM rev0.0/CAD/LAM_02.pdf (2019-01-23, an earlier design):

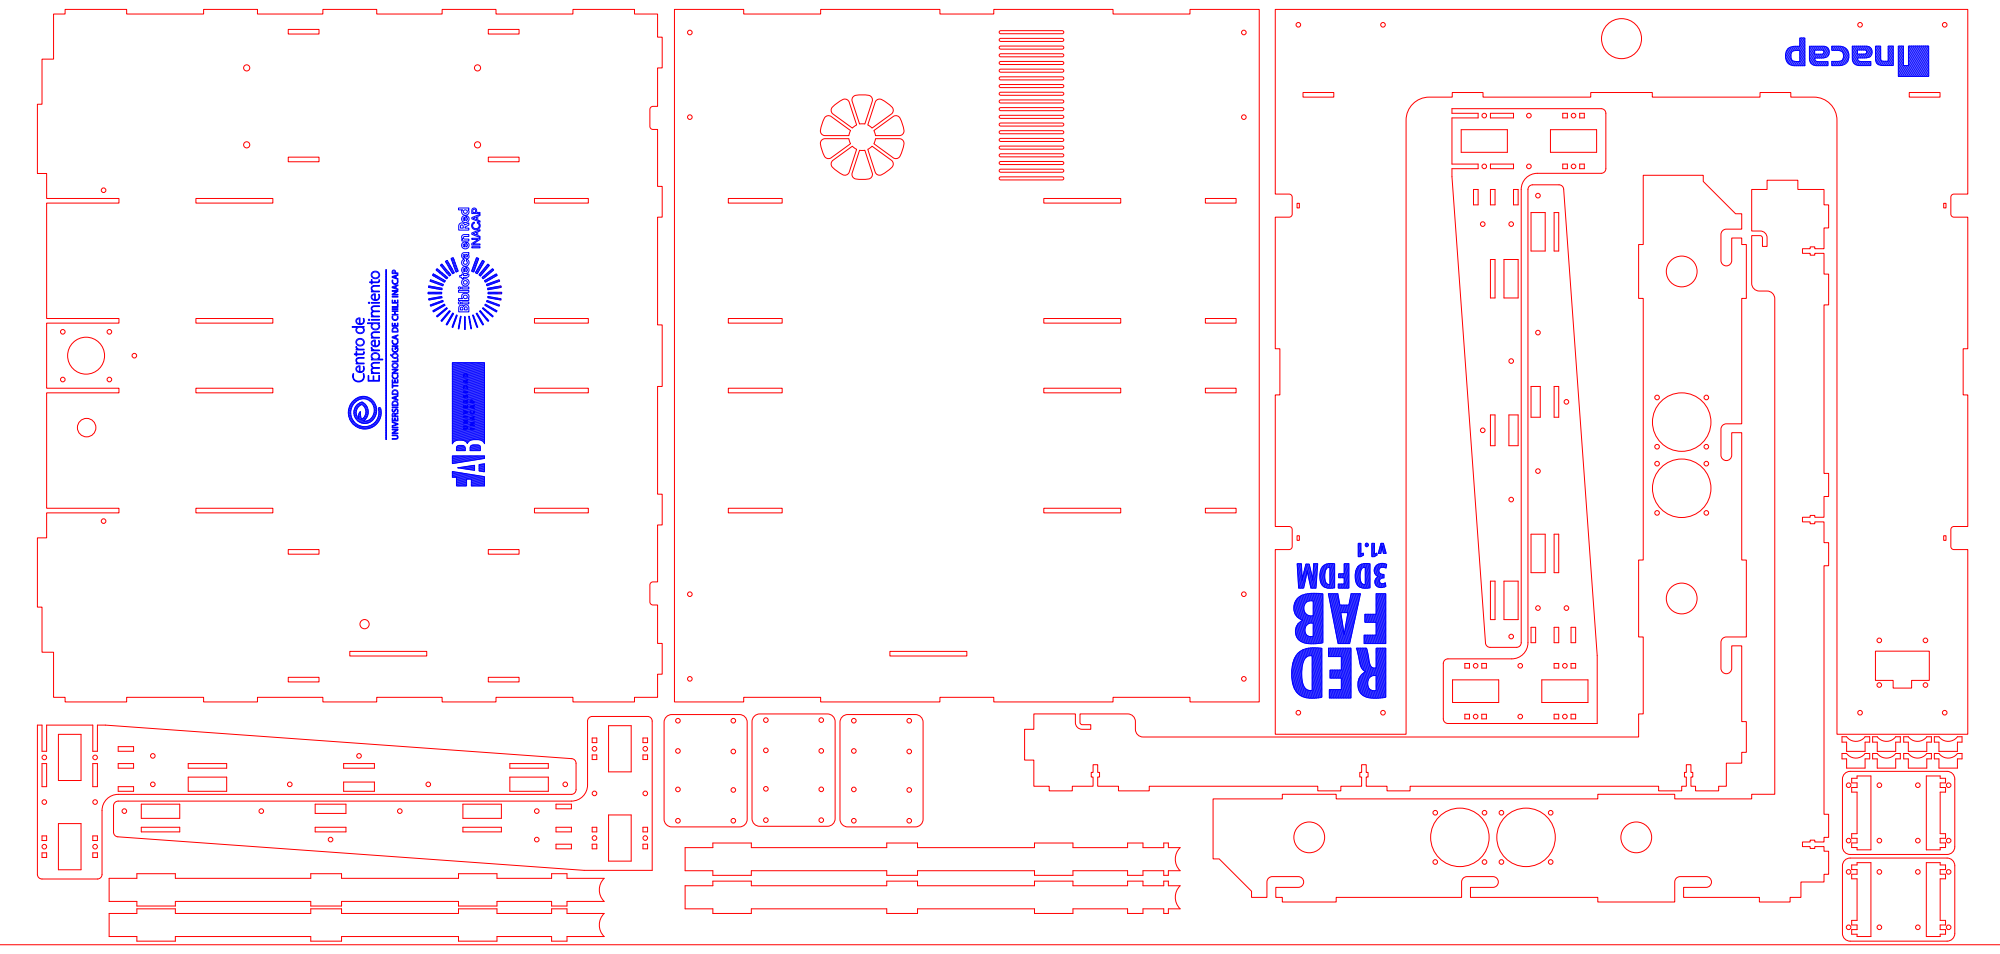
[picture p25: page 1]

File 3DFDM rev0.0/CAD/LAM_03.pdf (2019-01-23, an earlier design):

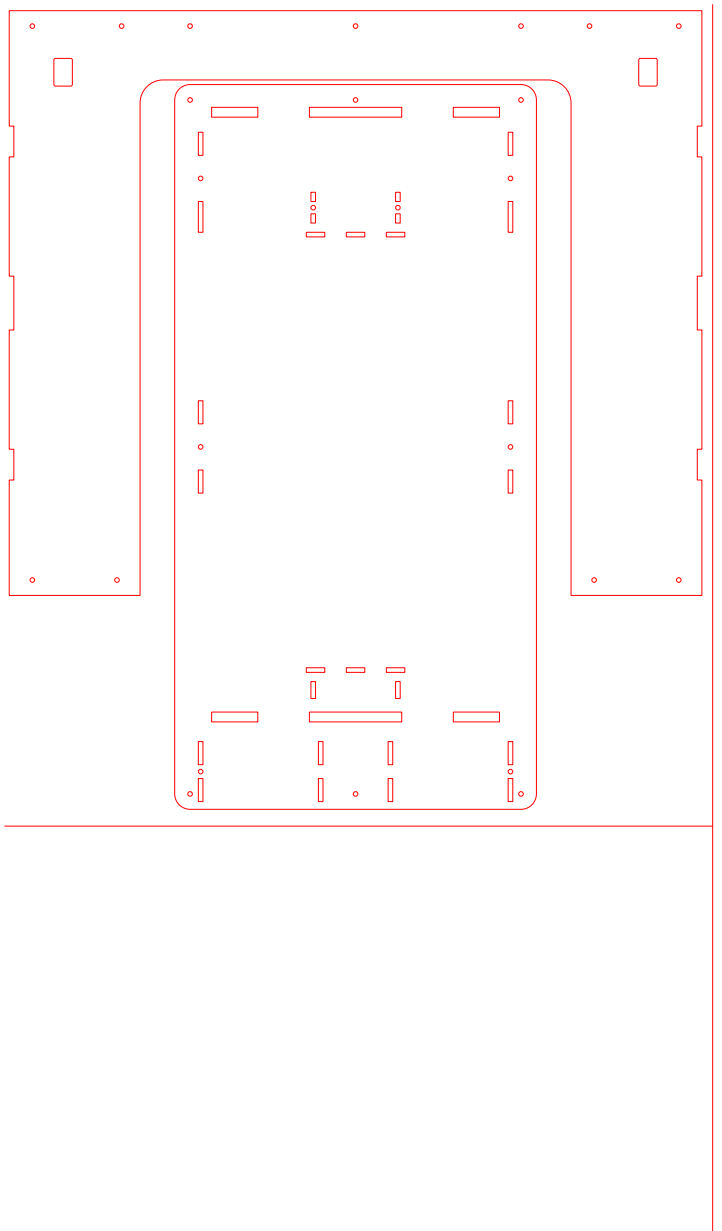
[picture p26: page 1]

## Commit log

2019-02-11 Marlin 2.0
    Esta versión de FW Marlin se encuentra modificada para trabajar con la REDFAB 3D FDM v1.1.
    Marlin es un firmware de código abierto para RepRap y otras impresoras 3D de modelado por deposición fundida (MDF) basadas en la plataforma Arduino.
    El firmware se ejecuta en el placa de control de la impresora 3D y administra todas las actividades en tiempo real de la máquina, incluido el movimiento a través de los controladores paso a paso, cal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
2019-07-01 Revisión 1.0 corte Laser
    1.- Se simplifica armado de la base eje Z.
    2.- Se cambia de ubicación de SD para mejorar montaje.
    3.- Montaje de electrónica se optimiza para armado.
2019-07-08 REDFAB V1.1 rev.1
    Actualización impresora REDFAB 3D FDM v1.1
    Se mejora base cama eje Z
    Se corrige sistema trasmisión eje Y
    Se cambia posición de Ramps y lector SD
2019-07-09 Revision 0.1 REDFAB 3D FDM
    Actualizacion de archivos STL
    [Carro_Cabezal.stl, Eje_X_Soporte_Motor.stl, Eje_X_polea.stl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]
2019-07-09 Actualizacion STL
    [4xUnion_Marcos_Inferior.stl, Clip cable.stl, Eje_Y_Frontal_V2.stl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]
2019-07-09 Se elimina carpeta
    [Eje_Y_Frontal_V2.stl, Eje_Y_Posterior_V2.stl, Soporte_Motor_v2.stl]
2019-07-09 Revision 0.1 REDFAB 3D FDM
    [Eje_Y_Frontal_V2.stl, Eje_Y_Posterior_V2.stl, Soporte_Motor_v2.STL]
2019-07-09 Create Marlin 2.0.txt
    Marlin 2.0 takes this popular RepRap firmware to the next level by adding support for much faster 32-bit and ARM-based boards while improving support for 8-bit AVR boards. Read about Marlin's decisio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
    This branch is for patches to the latest 2.0.x release version. Periodically this branch will form the basis for the next minor 2.0.x release.
2019-07-09 BOM REV0.1
    Se actualiza lista de materiales
2019-07-10 Corte Laser MDF3mm
    Optimizacion de corte, 2 formato de plancha 130x80cm
2019-07-15 1,3" OLED SH1106 Frame with Source (DesignSpark Mechanical)
    https://www.thingiverse.com/thing:3490816/files
    [OLED-Test.stl]
2019-07-15 3D FDM revision 0
    [Base_pantalla_Oled 1.3.stl, Carro.STL, Clip Bowden.stl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]
2019-08-06 Create Conector de Planos.stl
    [Conector de Planos.stl]
2019-09-09 BOM Actualizado
2019-09-11 Corte Laser MDF 3mm
    Correccion de lamina 1, pieza faltante
